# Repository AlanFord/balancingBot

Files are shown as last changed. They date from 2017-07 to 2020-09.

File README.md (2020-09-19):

# Balancing Bot
## Table of Contents
- [Introduction](#introduction)
- [The Remote Control](#the-remote-control)
	- [Wiring the Nunchuck](#wiring-the-nunchuck)
	- [Wiring the Transceiver](#wiring-the-transceiver)
	- [Putting It All Together](#putting-it-all-together)
	- [Powering It Up](#powering-it-up)
	- [Programming the Arduino](#programming-the-arduino)
- [The Bot](#the-bot)
	- [Hardware](#hardware)
		- [The Frame](#the-frame)
		- [The Motors and Wheels](#the-motors-and-wheels)
		- [Motor Control](#motor-control)
		- [Balancing](#balancing)
		- [Power](#power)
		- [Communications](#communications)
		- [The Blinky Lights](#the-blinky-lights)
		- [The Brains Behind it All](#the-brains-behind-it-all)
	- [Software](#software)
		- [Function List](#function-list)
		- [Timing Overview](#timing-overview)
		- [Battery Voltage Monitoring](#battery-voltage-monitoring)
		- [Attitude Monitoring](#attitude-monitoring)
		- [Wireless Communications](#wireless-communications)
		- [Serial Communications](#serial-communications)
		- [Motor Control Software](#motor-control-software)
		- [The Feedback Calculations](#the-feedback-calculations)
- [Operating the Balancing Bot](#operating-the-balancing-bot)
	- [Calibrating the Accelerometer](#calibrating-the-accelerometer)
	- [Starting up the Robot](#starting-up-the-robot)
	- [If Something Goes Wrong](#if-something-goes-wrong)

## Introduction
The Balancing Bot is a battery-powered two-wheeled balancing robot that can move under remote control.  The robot is built primarily from off-the-shelf parts.  The frame is plywood, easily made with hand tools or a small CNC router.  The robot’s electronics are based on an Arduino microcontroller and a combination gyro/accelerometer.  Communications with the remote control are performed over a 2.4 GHz wireless transceiver module.  The remote control is comprised of a repurposed Wii-compatible nunchuck controller, an Arduino microcontroller, and a 2.4 GHz wireless transceiver module.

This is a fork of the Joop Brokking's 
[balancing robot](http://www.brokking.net/yabr_main.html).
Many parts have been replaced with easier-to-obtain (for me) breakout boards from sparkfun.com, pololu.com, and amazon.com.

## The Remote Control
The primary component of the remote control is the Wii-compatible nunchuck.  The nunchuck joystick is used to maneuver the robot in right, left, forward, and backward movements.  The nunchuck is designed to communicate via a proprietary I2C connection.  Fortunately, it’s easy to communicate with the nunchuck using and Arduino Uno.  The Arduino programming environment provides a library (Wire) that implements the I2C communications protocol.

Getting the maneuvering commands from the remote control to the robot is performed using a Nordic Semiconductor nRF24L01+ 2.4 GHz wireless transceiver.  The communications protocol is proprietary, but the transceiver is available on a Sparkfun breakout board and communication is handled via the SPI and RF24 libraries.

Wiring the nunchuck to the Arduino can be plug-and-play if you use one of the various Wii nunchuck 
[breakout adapters](https://www.adafruit.com/product/345).  
However, the nunchuck can also be wired directly to the Arduino by removing the nunchuck connector.  This will be covered next.

### Wiring the Nunchuck
Removing the nunchuck connector reveals five wires, only four of which are required here - VCC (+3.3V), GND, SDA (data), and SCL (clock).  Unfortunately, the color of the various wires may change depending on the nunchuck supplier.  However, as a fallback the various wires can be identified by looking straight into the connector.  The wire layout would be as follows:

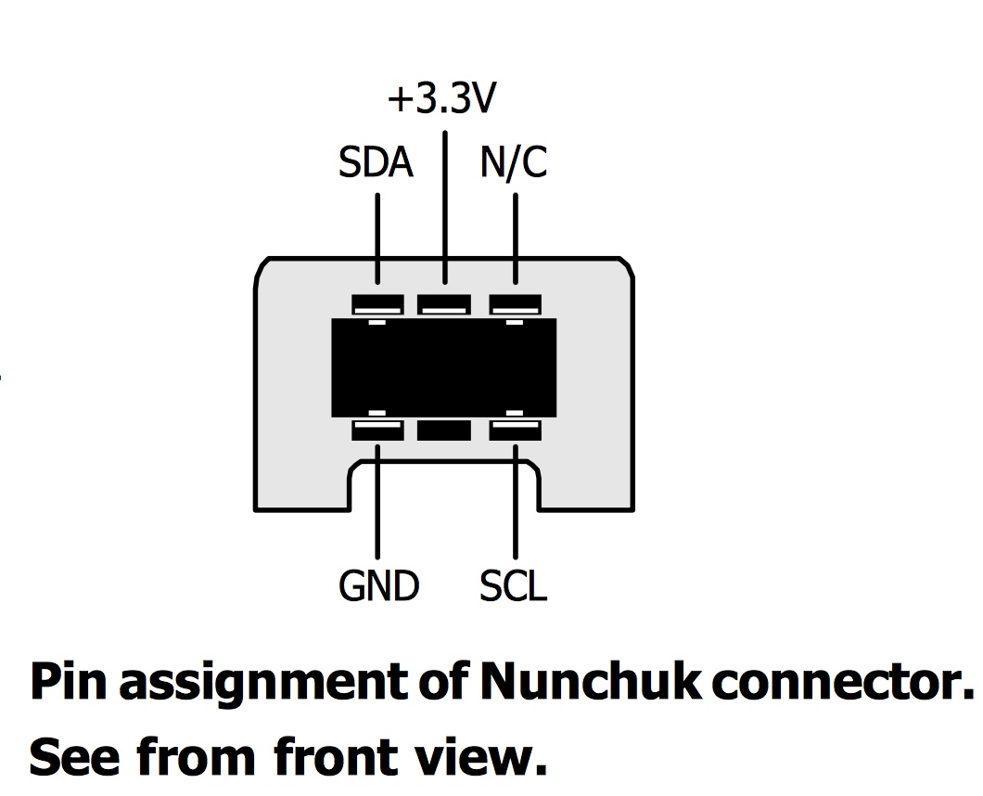
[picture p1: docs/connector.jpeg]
nunchuck-connector


Go ahead a cut off the connector and attach the wires to the following pins on an Arduino Uno – 

| Wii  | Arduino Pin |
| ---- | ---|
|SDA | A4 |
|SCL | A5 |
|+3.3V | 3V3 |
|GND | GND |

Note that the Wii nunchuck is a +3.3V device and the Arduino is a +5V device.  This is accommodated because an I2C connection is *open-drain*, i.e. the data lines (SDA and SCL) are nominally either grounded or floating.  The Wii nunchuck has internal pull-up resistors that will pull each data line up to +3.3V when either the Nunchuck or the Arduino is not pulling the line to ground during signaling.

However, the Arduino also contains internal pull-up resistors that are enabled by default and will attempt to pull the signal lines up to +5V.  While this appears not to damage the nunchuck, it would be more appropriate to disable the Arduino internal pull-up resistors and rely only on the pull-ups internal to the nunchuck.

### Wiring the Transceiver
The transceiver that I used was part of a Sparkfun breakout board that used an SPI interface.  The SPI interface requires more data lines than an I2C or serial connection.  The following are the required connections:

| Transceiver | Arduino Pin |
| --- | --- |
|CE | D9 |
|CSN | D10 |
|MOSI | D11 |
|MISO | D12 |
|SCK | D13 |
|VCC | 5V |
|GND | GND |
|IRQ | not used! |

### Putting It All Together
While all of those wires could be just attached to the Arduino Uno headers, it didn’t seem to make for stable connections.  In addition, it would be best if the wireless transceiver stood up vertically above the Arduino Uno to provide better radio reception.  My solution was to use an Arduino prototyping shield.  A female 8-pin header was soldered to the prototyping shield and a male right-angle 8-pin header was soldered to the transceiver board.  Plugging the transceiver into the female header on the prototyping shield allows the transceiver to stand upright above the Arduino Uno.  The nunchuck wires can be soldered directly to the appropriate locations on the prototyping shield.  I mounted the Arduino Uno on a 
[plastic mounting plate](https://www.adafruit.com/product/275)
 that provided an area to the side for securing the nunchuck cable with a cable tie and an adhesive-backed mounting base.

### Powering It Up
The remote control can be powered by a power supply with a barrel jack supplying between +9V and +12V.  Alternatively, it can be powered from a laptop via a USB connector.

To make the remote control more portable, it is possible to power it via a USB cable attached to a cell-phone battery pack.  Care must be taken to choose a batter pack that does not shut off when the current flow drops to about 20 mA (typical of the Arduino Uno).  If you have a battery pack that does tend to shut off, adding an LED to the Arduino that uses an additional 15 mA may keep the battery pack from shutting off.

### Programming the Arduino
The Arduino Uno program reads the state of the nunchuck joystick and transmits the state to the robot.  The Uno program is *Balancing_robot_remote.ino*.  When first powered up, the program initializes the microcontroller by making calls to the routines `initialize_serial()`, `initialize_radio()`, `initialize I2C()`, and `wake_nunchuck()`.  `initialize_serial()` inizializes a 9600 baud serial connection that can be optionally be used to monitor the state of the Uno.  `initialize_radio()` and `initialize I2C()` are self explanatory.  `wake_nunchuck()` initializes the I2C data communication with the nunchuck.  Of special interest are the lines in `initialize_I2C()` that disable the Arduino internal pull-up resistors.  This configuration permits safely connecting the +3.3V nunchuck with the +5V Arduino.  The relevant lines in `initialize_I2C()` are:

```cpp
Wire.begin();			//Start the I2C bus as master
digitalWrite(SCL, LOW);		//disable the pull-up on the SCL line
digitalWrite(SDA, LOW); 	//disable the pull-up on the SDA line
```

SCL and SDA are Arduino-defined constants referring to the appropriate pins.

Initializing the radio requires using a “pipe” address, or name. We need to ensure that the remote and the robot are on the same pipe address.  The pipe address is a five-character string – in this case “1robt”.

Communicating with the nunchuck consists of sending 0x00 to the nunchuck followed by a request for six bytes of data.  The first byte of data received represents the left/right position of the joystick, with the values varying from 0 to 255 (full left to full right).  The second byte of data received represents the front/back position of the joystick, with values varying from 0 to 255 (full reverse to full forward).  Ignoring a dead zone of 80 to 170 (to avoid jitter and noise), the nunchuck data is converted to robot commands of BOT_LEFT, BOT_RIGHT, BOT_FORWARD, and BOT_REVERSE.  The commands are represented by the following byte encoding:

```
BOT_LEFT            B00000001
BOT_RIGHT           B00000010
BOT_FORWARD         B00000100
BOT_REVERSE         B00001000
BOT_STABLE          B00001100
```

The values can be combined by ORing the bytes together.  For example, to move forward and turn right simultaneously the values of BOT_FORWARD and BOT_RIGHT would be ORed together to form a command byte of B00000110.

The command byte is then broadcast via the transceiver using the library call radio.write(). After a delay of 40 milliseconds the process is repeated.

## The Bot
It takes a lot to keep the robot upright and doing it’s job.  The robot runs on two wheels, powered by one stepper motor for each wheel.  Controlling the direction of wheels independently allows the robot to roll forward, roll backward, turn right, turn left, or a combination of these.  In addition to the overall motion of the robot, the wheels are also used to balance the robot.  If the accelerometer indicates that the robot is tipping forward or backward, the wheels are driven to move the wheels in the direction of the tilt, effectively moving the robot body into an upright positon.  The ability to do this without having the top of the robot flailing around requires that a weight be added to the top of the robot, simulating an “inverted pendulum”.  In this case the weight is implemented by mounting a large lithium-polymer (LiPo) battery on the top of the robot frame.  Beyond helping balance the robot, the size of the LiPo batter also provides a substantial power supply for the robot’s electronics and motors.

The robot also needs computing power, but an Arduino Uno (the microcontroller used in the remote control) is too large to use on the robot.  Instead, an Arduino Pro Mini is used.  The Pro Mini is significantly smaller and comes in 3.3 V and 5 V versions.  Only the 5V version should be used, as 5V is need to interface with some of the electronics.  This will be covered in more detail later.

### Hardware

#### The Frame
Wood.  Just wood.  Well, maybe a little fancier than usual.  The frame is built out of  “baltic birch” plywood.  This plywood has more plies (layers) than your average plywood, making it stronger, flatter, etc.  The various pieces of the frame are held together with wire brads from a brad nailer.  Hand nailing will work also.

#### The Motors and Wheels
The robot moves because of stepper motors attached to wheels.  The stepper motors used in this project are NEMA 14-size bipolar motors from STEPPERONLINE (part number 14HS13-0804S).  The motors had the following characteristics:

```
18 N-cm (25.5 oz.-in) holding torque
1.8 degree stepper angle (200 steps/rev)
5.4V, 0.8A
6.8 ohms
5 mm shaft diameter
24 mm shaft length
```

The motors are mounted directly to the wooden robot body using the four threaded mounting holes found on the face of all NEMA stepper motor bodies.

Wheels can be found from many sources or may be repurposed from old toys.  The wheels used in this project were 60mm x 8mm with silicone tires.  The wheels were mounted to the stepper motor shafts using Pololu aluminum mounting hubs sized for a 5mm stepper shaft.

#### Motor Control
The stepper motors are controlled by stepper motor drivers, one per motor.  The stepper motor drivers receive motor positioning signals from a microcontroller and convert them into motor coil currents to control the motors.  This design uses two of the Pololu A4988 Stepper Motor Driver.  This driver can operate from 8 V to 35 V and can deliver up to 1 A per phase without a heat sink.  Microstepping down to 1/16-step is available.  VDD can be in the range of 3 V – 5.5 V.  Current limiting (the motors in use can only take 800 mA) is performed by adjusting an on-board trimmer potentiometer.  After adjusting the potentiometer, the current limit is

```
Current limit = VREF / (8 x 0.068 ohms)
```

where VREF is the voltage on the trimmer dial (measure by lightly touching – pressing down can change the trimmer pot adjustment!) or at the neighboring via.  For example measuring 0.5 V with a reference voltage of 5 V would mean a current limit of 0.919 A.  As the motors can take a maximum of 800 mA, the measured voltage should never be greater than 0.435 V, assuming a reference voltage of 5 V.  The original design indicates a current limit of 150 mA was to be used.  The modified design used here needs about 500 mA to power the motors such that they will hold position.

The following is a general depiction of how the motor driver should be wired.

![A4988]

Additionally, the \~ENABLE pin should be raised to the logic power supply voltage to disable the driver.  MS1, MS2, and MS3 
can be used to control microstepping as follows:

| MS1  | MS2  | MS3  | Microstep Resolution |
| ---- | ---- | ---- | --- |
| Low  | Low  | Low  | Full step |
| High | Low  | Low  | Half step |
| Low  | High | Low  | 1/4 step |
| High | High | Low  | 1/8 step |
| High | High | High | 1/16 step |

The motor drivers used in the robot are wired as follows:

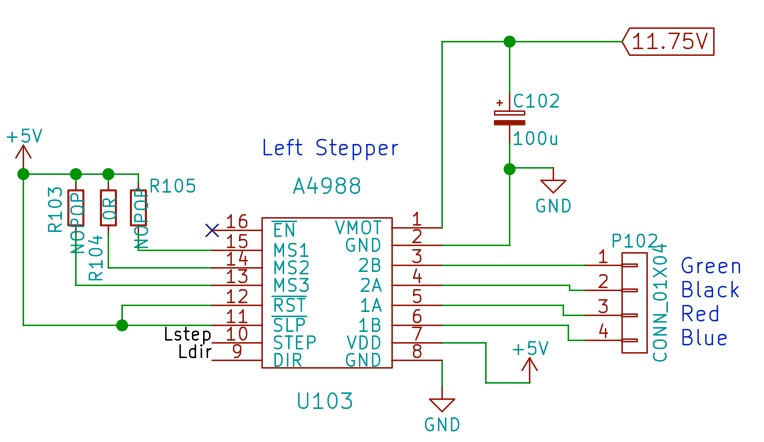
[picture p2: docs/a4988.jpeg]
A4988-wiring


Only MS2 is High, so the microstepping is set to ¼ step.  The \~ENABLE line is not connected; hence the stepper driver is always enabled.  The STEP and DIR pins are connected to the following Arduino Pro Mini pins:

|            | Arduino Pins | Arduino Pins |
|            | for          | for          |
| Driver Pin | Left Motor   | Right Motor  |
| ---------- | ------------ | ------------ |
| STEP       |	D4          | D2           |
| DIR        |	D5          | D3           |

#### Balancing
Balancing of the robot is performed by monitoring the gyro/accelerometer.  The gyro/accelerometer is implemented using a MPU-6050 six-axis sensor on a GY-521 breakout board.  The GY-521 communicates over I2C and can be powered with between 3.3V and 5V.

Care should be taken when mounting the GY-521 to the robot.  The accelerometer X-axis should be the vertical axis with the Y-axis pointing to the left as you face the front of the robot.  Mounting in other orientations will require software changes.

Wiring up the GY-521 is straight forward – 

| GY-521 | Arduino Pro Mini Pin |
| --- | --- |
| SDA | A4 |
| SCL | A5 |
| VCC | 5V |
| GND | GND |

#### Power
Power ultimately comes from a 3S LiPo battery, used not only for power but also to add weight to the top of the robot for balancing.  Power control and polarity are provided by a toggle switch and a diode.  The battery voltage is regulated down to 5V using a D24V10F5, 5V, 1A step-down voltage regulator available from pololu.com.  5V is then supplied to all of the on-board electronics.  The +11.75V output of the diode is supplied to the motor drivers to power the stepper motors.  The following summarizes the power supply:

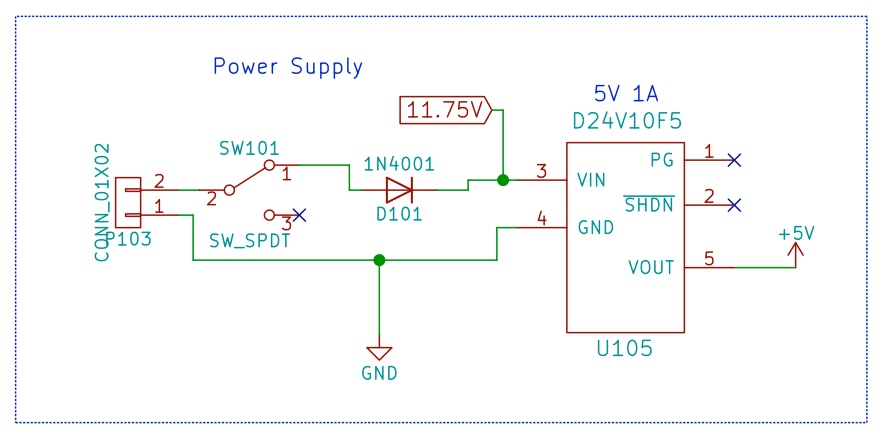
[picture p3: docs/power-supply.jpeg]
power-supply


#### Communications
The robot uses the same nRF24L01+ 2.4 GHz wireless transceiver used by the remote control.  The following are the required connections:

| Transceiver | Arduino Pin |
| --- | --- |
| CE | D09 |
| CSN | D10 |
| MOSI | D11 |
| MISO | D12 |
| SCK | D13 |
| VCC | 5V |
| GND | GND |
| IRQ | not used! | 

#### The Blinky Lights
One status LED is used on the robot.  A red LED is connected is series with a 330 ohm resistor between the Arduino D17 pin and ground.  Of course, I forgot to add this LED originally so my robot has it bodge-wired into place.  

The LED is first used when the robot is initially powered on.  The robot should be laying on it’s back when the power switch is toggled.  The LED will begin blinking as the accelerometer is calibrated.  Once the blinking stops, slowly rotate the robot to vertical and it will stabilize.

The other use of the LED is to warn when the battery voltage is too low.  The LED will turn on continuously when the battery voltage drops below +10.5V.  At this point the motors will also be de-energized and the robot will stop.

#### The Brains Behind it All
Integrating the robot parts is the job of the Arduino Pro Mini.  The Arduino Pro Mini comes in both a 3.3V and 5V version, but the 5V version should be used here so the voltage is consistent with the supply voltage used by the transceiver and the motor drivers.

### Software
The Arduino provides several functions, namely attitude monitoring, motor control, communications with the remote, and battery voltage monitoring.  These will be described in the following sections.  As an introduction though, it should be clear that the Arduino separates work into two categories – setup and loop.  Work performed in the setup occurs only once after power-up.  Work performed in the loop is repeated until the robot is powered down.  Some of the robot functions are performed in the setup and some are controlled by the loop.

#### Function List
- Balancing_robot.ino
  	- void setup(), the Arduino setup routine
	- void loop(), the main Arduino control loop
- misc.ino
	- void initialize_i2c(), initialize the i2c bus to communicate with the remote
	- void initialize_timer(), initialize the timer used with the interrupt service
	- bool battery_voltage_is_low(), determine if the battery voltage is too low
- gyro.ino
	- void initialize_gyro(), initialize the gyro/accelerometer
	- void calibrate_gyro(), initial gyro calibration
	- void get_gyro_angle(), determine the gyro's estimate of the vertical angle
	- float get_accelerometer_angle(), determine the accelerometer's estimate of the vertical angle
- radio.ino
	- void initialize_radio(), initialize the RF24 radio transceiver
	- byte get_radio_data(), get a byte of data from the remote control
- pid.ino
	- float pid_calculator(), determine the pid feedback value
	- void direction_control(), add user direction signal to pid feedback value
	- void calculate_motor_pulse_interval(), conver pid result to motor period
- isr.ino
	- ISR(), drive the stepper motor based on requested motor period

#### Timing Overview
The various processes that make up the control software work on a number of timing intervals.

- The remote control has a primary timing loop that is executed once every **40 milliseconds**.  This is the
frequency at which the handheld controls are polled for updates and new data are transmitted to the robot.
- Data received from the remote control by the robot is considered valid for only **100 milliseconds** if no other data is received.  After that time it is discarded.  This avoids the issue of using old, invalid commands when the radio link is interrupted.
- The robot has a primary timing loop that is executed once every **4 milliseconds**.  This timing loop 
controlls the frequency at which the gyro is checked, incoming remote control commands are logged, 
and balancing control calculations are updated, and motor speeds are determined.
- The time interval for the primary timing loop is also used to calculate the change in robot angle during the last loop interval (**4 milliseconds**).  The gyro only determines the *rate* of change in the angle.  The time interval is used to determine the change in the angle.
- The interrupt routine that drives the motors executes every **20 microseconds**.  The stepper motor drive 
period is comprised of one interrupt period executing a motor step followed by several non-stepping interrupt periods.

#### Battery Voltage Monitoring
The battery voltage is being monitored on pin A0, an analog input.  The nominal voltage for a 3S LiPo battery is +11.1 V, a maximum voltage of +12.6 V, and the minimum operating voltage is 9.9 V.  There is a diode in the battery circuit to prevent hooking the battery up with the wrong polarity.  The voltage drop across the diode is approximately 0.85 V.  Hence the remaining maximum voltage is +11.75 V and the minimum voltage would be +9.05 V.  Unfortunately the Arduino can only measure voltages between 0 V and 5 V.  Two resistors can be used to create a voltage divider to reduce the voltage to no greater than +5V.  The maximum voltage needs to be divided by at least (+11.75 V)/(+5 V) = 2.35.  Using readily available resistor sizes, a voltage divider can be made from 33K ohm and 21.5K ohm resistors, for a divider of (33K + 21.5K)/21.5 = 2.535.  Now the maximum voltage would be +11.75 V/2.535 = +4.64 V.

When reading the A0 pin, the Arduino generates an integer value of 0 for 0V and 1023 for 5V, or 0.00489 V per division.  Thus the integer generated from reading the pin would be

```
A0 = (battery voltage – 0.85V)/2.535/(0.00489V/division), or
A0 = (battery voltage * 80.67) – 68.57
```

Now, reading A0 with values between 0 and 1023, it’s hard to tell what the voltage really is.  So flipping the equation around and multiplying by 1000 (to get millivolts), we get

```
voltage reading = (A0+68.57)/80.67*1000 = A0*12.4 + 850
```

If the voltage reading drops below 10500 (+10.5V) the LED is turned on and the motors are de-energized.  The batter check is performed in the main loop of the Arduino software, executed on a 4 millisecond interval.

#### Attitude Monitoring
So why include both gyro and an accelerometer?  The gyro can determine the rate at which the robot is rotating (i.e. falling).  How is the gyro used to determine the angle of the robot?  The gyro’s value for rotation (degree/sec) is multiplied by the time since the last check to determine how much the robot’s angle has changed over that time.  But changed from what?  The gyro can’t determine what angle the robot started at.  This is where the accelerometer comes in.  When the robot is moved to an upright position, the accelerometer can tell from the gravitational pull how close the robot is to vertical.  Once the robot is close to vertical the angle calculated from the accelerometer is used to initialize the gyro’s ongoing, updated angle calculations.  Voila!

The gyro/accelerometer (henceforth referred to as the gyro) is initialized in the Arduino’s setup() function.  The gyro operating mode is set to 250 degree/sec full scale for the gyro and +/- 4g full scale for the accelerometer.  Both the gyro and accelerometer functions return a signed 16-bit integer.  The accelerometer has a sensitivity of 8192 LSB/g.  The gyro has a sensitivity of 131 LSB/degree/sec.

The gyro yaw and gyro pitch values are read from the gyro and then the program is paused for \~4 milliseconds.  This is repeated for a total of 500 times and the resulting yaw and pitch values are averaged over the 500 values.  The resulting average yaw and average pitch are the gyro calibration values.

In the main loop the gyro angle is initialized to equal the accelerometer angle only once, at the beginning of operation when the robot is standing vertical.  The gyro angle is then updated once every \~4 milliseconds (the loop time for the main program loop).

#### Wireless Communications
As with the remote control, communications with the wireless transceiver is done with the SPI bus.  As with the remote control, the radio is initialized with a pipe address of “1robt”.  Interestingly, while the radio can transmit on only one pipe, it can receive on six pipes simultaneously.  Thus when initializing the radio we must also specify a pipe number, in this case “1”.    Wireless communications occur in the main loop of the Arduino software, executed on a 4 millisecond interval.

#### Serial Communications
Serial communications can be enabled at compile-time by defining the macro SERIALCOMM.  Serial communications are then initiated at 9600 baud (slow enough not to impede the other work being done).  Serial communications occur over the USB connection.

#### Motor Control Software
Motor control is not done in either of the normal Arduino functions setup() or loop().  Instead, motor control is performed in an interrupt handler.  The Arduino has built-in timers that can cause the microcontroller to perform operations on a repeating fixed interval.  One of the ways this can be done is to associate a special program (i.e. a function) with the timer.  Such a program/function is referred to as an interrupt handler.  The robot uses Timer 2 to perform motor control on an interval of every 20 microseconds.  The motor control is performed by a function called ISR(TIMER2_COMPA_vect).  Timer 2 is initialized in the standard Arduino setup() function.

Moving the stepper motor by one step (or by a ¼ step in this configuration) a pulse is generated on the appropriate input pins for the stepper controllers.  This is done by pulsing Arduino Pro Mini pin D2 for the right motor and pin D4 for the left motor.
Some caution is needed when controlling the direction of the stepper motors.  The stepper motors and drivers are configured symmetrically with respect to the Arduino Pro Mini.  However, the left motor is rotated 180 degrees when mounted on the robot.  Thus, the right motor will go forward when Arduino pin D3 is high and reverse when pin D3 is low.  The left motor is reversed, going forward when Arduino pin D5 is low and reversing when pin D5 is high.

Manipulating the Arduino Port D pins for motor stepping and direction is made a little easier by the constants defined in the Arduino program:

```cpp
const uint8_t LEFTMOTORDIR     = (0b00000001 << 5);
const uint8_t LEFTMOTORSTEP    = (0b00000001 << 4);
const uint8_t RIGHTMOTORDIR    = (0b00000001 << 3);
const uint8_t RIGHTMOTORSTEP   = (0b00000001 << 2);
```

#### The Feedback Calculations
The feedback calculations are designed to continuously update the motor positioning required to accomplish several (sometimes mutually exclusive) goals simultaneously.  The goals are:
 - Keep the bot vertical and stable when not moving.  This is accomplished by adjusting the variable `self_balance_pid_setpoint`

 - Incorporate necessary changes when the remote control requests a turn.  This accomplished by setting the variables `pid_output_left` and `pid_output_right` to be +/- `turning_speed`.  The sign is adjusted to make the wheels turn in opposite directions, spinning the robot in place.  The `turning_speed` variable is a predefined constant (20).

 - Incorporate changes when the robot is to move forward or backward.  To move forward, the robot is leaned forward by adjusting pid_setpoint in 0.005 increments each time the main loop is executed (4 millisec) until the maximum speed `max_target_speed` (150) is reached.

  - If the robot is more than 30 degrees from vertical (i.e. it fell over), shut the motors down and reset the feedback calculations.

  - When the robot is not at the required angle from vertical, calculate a new.

As was mentioned in the Motor Control section, the interrupt handler is executed every 20 microseconds.  The motor step pulse is activated in one interrupt and deactivated in the next.  Thus, the minimum pulse period (the full cycle) is 40 microseconds and the step frequency is 25,000 steps/sec.  The motors are nominally 200 steps/rev and the motor controllers are set for ¼ microstepping, so the maximum speed of the robot is 

```
(25,000microsteps/sec)(1step/4microsteps)(1rev/200steps) = 31.25 revolutions/sec
 ```

The wheels/tires have a diameter of 60 mm, resulting in a maximum linear speed of

```
31.25 rev/sec * (pi * 60 mm) = 5890.5 mm/sec = 19.3 ft/sec.
```

`throttle_left_motor` and `throttle_right_motor` are generated by the feedback calculations to control the motor.  They contain the number of 20 microsecond intervals between the pulses used to move the stepper motor.  A counter for each motor counts up to the throttle value from 0.  On 0 the stepper pulse is created and on 1 the stepper pulse is ended, giving one 20 microsecond pulse followed by a (throttle-1) * 20 microsecond delay.  A negative value of throttle_left_motor or throttle_right_motor will cause the motor to reverse.

In summary, it’s important to remember that the value generated by the feedback calculations is the *delay* between stepper motor steps.

## Operating the Balancing Bot

### Calibrating the Accelerometer
This really only has to be done once, so I’m putting it in a separate section of the documentation.

### Starting up the Robot
It’s pretty simple; just follow these steps:

 1.	Power up the remote, either using a wall wart or a battery pack
 2.	Lay the robot on it’s back on a flat surface.
 3.	Flip the toggle switch to power-up the robot.
 4.	Wait for the gyro/accelerometer to calibrate (the red LED will stop blinking)
 5.	Gently rotate the robot to a vertical position
 6.	Turn it loose and start driving it around!

### If Something Goes Wrong 
If the robot falls down because it ran into something, just pull it back upright and it should stabilize itself.

If, during operation, the red LED turns on, the motors will de-energize because the LiPo battery voltage has dropped too low.  Flip the toggle switch to turn off the robot, swap in a new battery, and begin again!

<!-- Images -->
[nunchuck-connector]:   ./docs/connector.jpeg      "Nunchuck connector wiring"
[A4988]:                ./docs/basic.png           "A4988 diagram"
[A4988-wiring]:         ./docs/a4988.jpeg          "A4988 wiring diagram"
[power-supply]:         ./docs/power-supply.jpeg   "Power supply diagram"

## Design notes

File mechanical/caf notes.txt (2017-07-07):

Website: http://www.brokking.net/yabr_main.html

Board List
==========
Arduino pro mini, 1, https://www.amazon.com/Arduino-Pro-Mini-328-3-3V/dp/B004G53J6M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
Arduino Uno, 1 [already in hand?]
FTDI USB to TTL programmer for Arduino pro mini, 1, [already in hand?]
MPU-6050 gyro and accelerometer, 1, https://www.amazon.com/Kootek-MPU-6050-MPU6050-sensors-Accelerometer/dp/B008BOPN40
2.4G wireless serial tranceiver module, 2
Geeetech StepStick DRV8825, 2, https://www.pololu.com/product/2133
Mini DC 7~28V to DC 5V step-down converter, 1

Hardware
========
Stepper Motor, 2
Wired nunchuck controller for Wii, 1, https://www.amazon.com/Supersaving360-Nunchuck-Nunchuk-Controller-Nintendo/dp/B00JFOZX3Q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
11.1V 2200mAh 30C Li-polymer Battery, 1, https://www.amazon.com/Battery-Helicopter-Quadcopter-Multirotor-EFLB22003S30/dp/B013TK47VK
B3AC 2s/3S Lipo balance charger

Details
=======
Stepper Motors
	Nema 14
	1.8 Degree step angle
	Bipolar (equivalent to 2 phase?)
	3.6V DC
	1.2A/phase
	8.8 ohms/phase
	3.5 mH
	185 mN.m Min holding torque (18.5 Ncm) (26 oz-in)
	31 g.cm2 rotor torque
	190g (6.7 oz)
	Brand:  Geeetech Model 35BY
	1.39in x 1.39 in x 2.48 in

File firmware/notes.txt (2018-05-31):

Changes from the original design:
1) Using SPI to communicate with the wireless card.  This will require use of arduino
	pins D10, D11, D12, and D13.
2) Need to solder up another LED.  The on-board LED is attached to the ATMEGA328 pin 17 
	(PB5) (SCK), which is wired to pin 9 of JP6.  This appears to be labeled on the 
	Arduino Pro Mini board as D13.
3) The voltage divider was redone, so the constants in the code should be altered.
4) Serial to the PC may be available since the wireless link isn't using it.

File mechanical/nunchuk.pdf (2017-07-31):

## Wii

## Nunchuk

## Interface

The

Wii

Nunchuk

uses a

proprietary

connector

with

six pins.

The

connections

are

as
follows.

Figure

1:

Wii

Nunchuk

Pinout
To

communicate

with

the

Nunchuk,

we

must

send

a

handshake

signal.

If

you

are
using

a

black Wii

Nunchuk,

send 2

bytes

0xF0, 0x55 to

initialize the first

register
and

0xFB, 0x00 to

initialize

the

second

register

of

the

Nunchuk.

On

a

white

Wii
Nunchuk,

send

0x40, 0x00 followed by 0x00. The I²C

address

of

both

Wii

Nunchuks
is

0x52.

The

frequency

used

to

communicate

with

the

Wii

Nunchuk

is

100KHz.

1 3 5
2 4 6
1 = +3V (3V recommended but works at 5V) | 2 = Clock
3 = N/A | 4 = N/A
5 = Data | 6 = Gnd

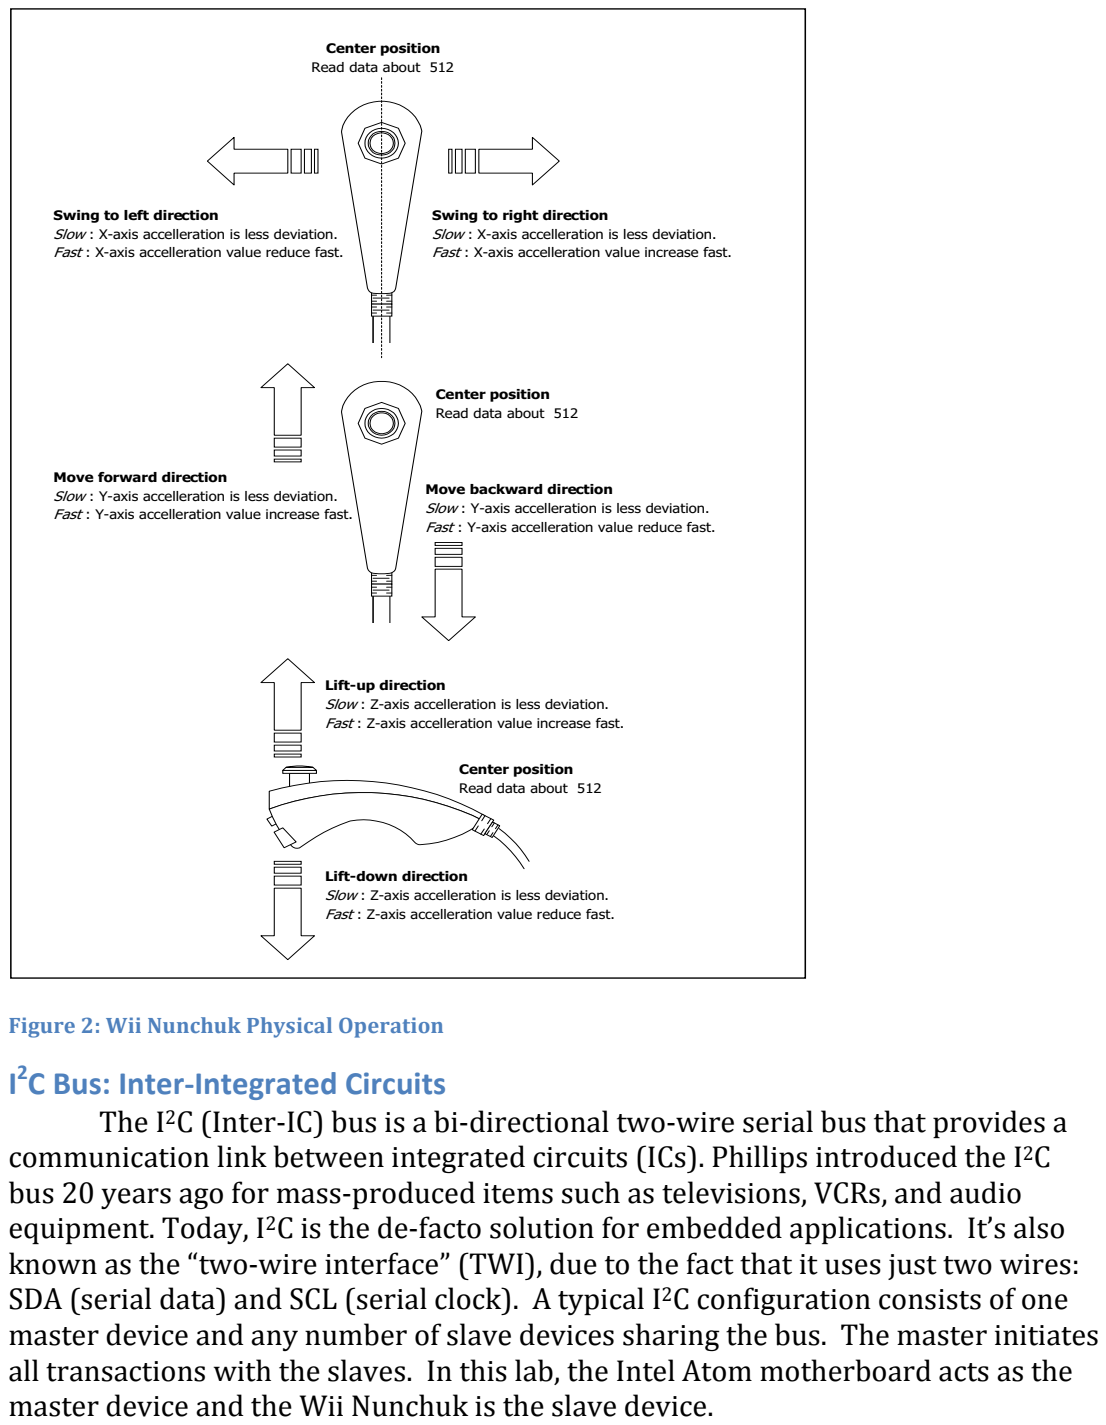
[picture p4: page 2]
Figure; Wii; Nunchuk; Physical; Operation; Bus:; Inter-‐Integrated; Circuits; The; I²C; (Inter-‐IC); bus; bi-‐directional; two-‐wire; serial; bus that; provides; communication; link; between; integrated; circuits; (ICs).; Phillips; introduced; the; years; ago; for; mass-‐produced; items; such; televisions,; VCRs,; and; audio; equipment.; Today,; de-‐facto; solution; embedded; applications.; also; known; “two-‐wire; interface” (TWI),; due; fact; that; uses; just; two; wires:; SDA; (serial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

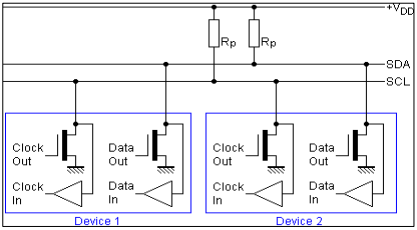
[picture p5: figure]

Another

name

you

will

hear

used

in

connection

with

I²C

is

SMBus (System
Management

Bus).

The

SMBus

protocol

was

developed

by

Intel

in

2005 and

is

based
on

I²C.

SMBus

defines

a

stricter

range

of

operating

limits,

including

clock

speed,
timing

and

data

formats,

compared

to

I²C.

Many

I²C

devices

have,

in

turn,
incorporated

policies

from

SMBus

and

both

kinds

of

devices

can

often

be

used

on
the

same

bus.

Figure

3:

I²C

Device

Circuit

Wii

Nunchuk

Output

The

Wii

Nunchuk

is

a

slave

I²C

bus

device

that

outputs

six

bytes

of

data

as
follows.

Figure

3:

Wii

Nunchuk

I²C

Output

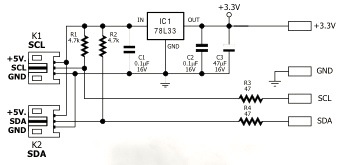
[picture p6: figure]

Figure

4:

Nunchuk

Interface

Board

Circuit

!&!!

!&!"

!&!'

!&!(

!&!)

!&!*

+,-./01234

+,-./01235

6117879,:7/79343;<0/3=3/,3<0/3'3>,93"!?<0/397.,8@/0,AB

6117879,:7/79353;<0/3=3/,3<0/3'3>,93"!?<0/397.,8@/0,AB

6117879,:7/793C3;<0/3=3/,3<0/3'3>,93"!?<0/397.,8@/0,AB

61178D3C
<0/3"

61178D3C
<0/3!

61178D35
<0/3"

61178D35
<0/3!

61178D34
<0/3"

61178D34
<0/3! | E?<@//,A | C?<@//,A
GH/H3<-/7397170I7 | 6FF97..
Byte 0x00 : | X-axis data of the joystick
Byte 0x01 : | Y-axis data of the joystick
Byte 0x02 : | X-axis data of the accellerometer sensor
Byte 0x03 : | Y-axis data of the accellerometer sensor
Byte 0x04 : | Z-axis data of the accellerometer sensor
Byte 0x05 : | bit 0 as Z button status - 0 = pressed and 1 = release
| bit 1 as C button status - 0 = pressed and 1 = release
| bit 2 and 3 as 2 lower bit of X-axis data of the accellerometer sensor
| bit 4 and 5 as 2 lower bit of Y-axis data of the accellerometer sensor
| bit 6 and 7 as 2 lower bit of Z-axis data of the accellerometer sensor

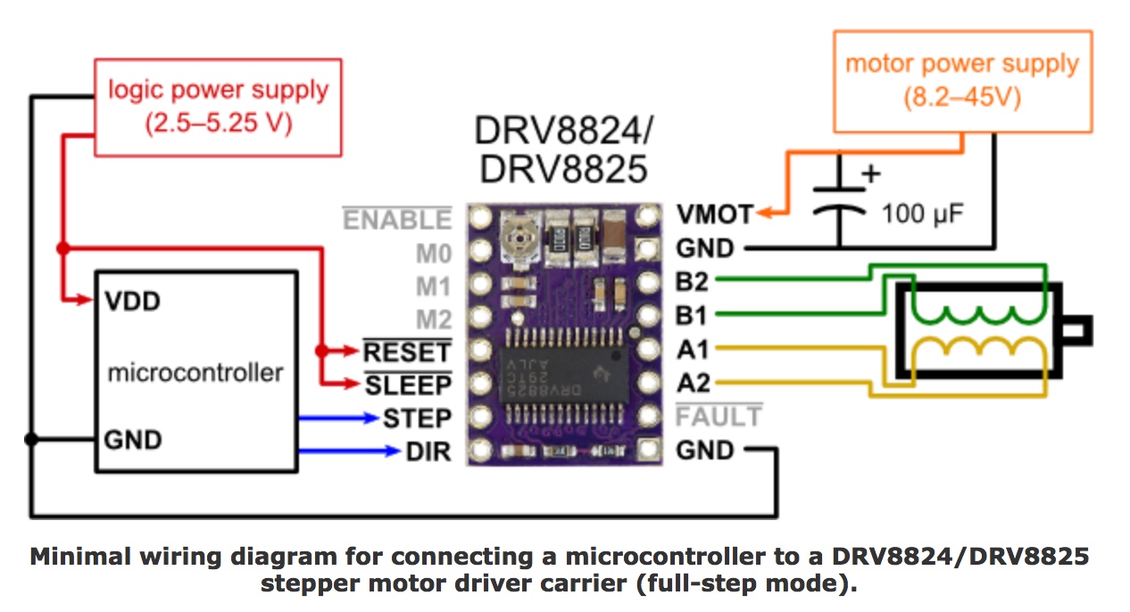
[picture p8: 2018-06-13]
docs/motor-driver.jpeg

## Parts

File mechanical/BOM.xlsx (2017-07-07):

 | Balancing Bot BOM
Count | Description | Part No. | Supplier | Status | Comment
1 | Arduino pro mini | DEV-11113 | sparkfun.com | basket | 5V, 16MHz, already own one?
1 | FTDI USB to TTL programmer |  |  |  | already own one?
1 | Arduino Uno |  |  |  | already own one?
1 | MPU-6050 gyro and accelerometer | B008BOPN40 | amazon.com | ordered | Kootek GY-521
2 | 2.4G wireless serial transceiver | WRL-00691 | sparkfun.com | received | nRF24L01+
2 | 35mm Stepper motor | B00PQ4Y9B6 | amazon.com | ordered | 0.8A/phase, 6R8, 18Ncm, 34mm long
2 | DRV8825 stepper driver | 2133 | pololu.com | ordered | 1.5A may be overkill
1 | wired nunchuck controller for Wii | B00JFOZX3Q | amazon.com | ordered
1 | 7-28V to 5V DC step-down converter | 2858 | pololu.com | ordered
1 | 11.1V 2200mAh 30C LIPO battery | B0072AEY5I | amazon.com | ordered | Turnigy 2200mAh 3S 20C Lipo, 6.6 oz, 103 x 33 x 24mm
1 | B3AC 2S/3S Lipo balance charger | 2588 | pololu.com | ordered | iMAX B6AC V2 Balance Charger - does it have the correct connector?
1 | PCB
1 | 3-pin toggle switch
1 | 2k2 resistor
1 | 3k3 resistor
1 | 4k7 resistor
1 | 1N4001 diode
1 | wheels (2) | 1421 | pololu.com | ordered
1 | wheel hardware (2) | 1203 | pololu.com | ordered | #4-40 screws not included
assorted | wood, 1/2"
assorted | wood, 1/8"
assorted | acrylic, 1/8"
 | standoffs
 | bolts
 | velcro tie-down
1 | arduino charger |  |  |  | already own one?
1 | LIPO batter tester monitor | B013U1CP08 | amazon.com | ordered

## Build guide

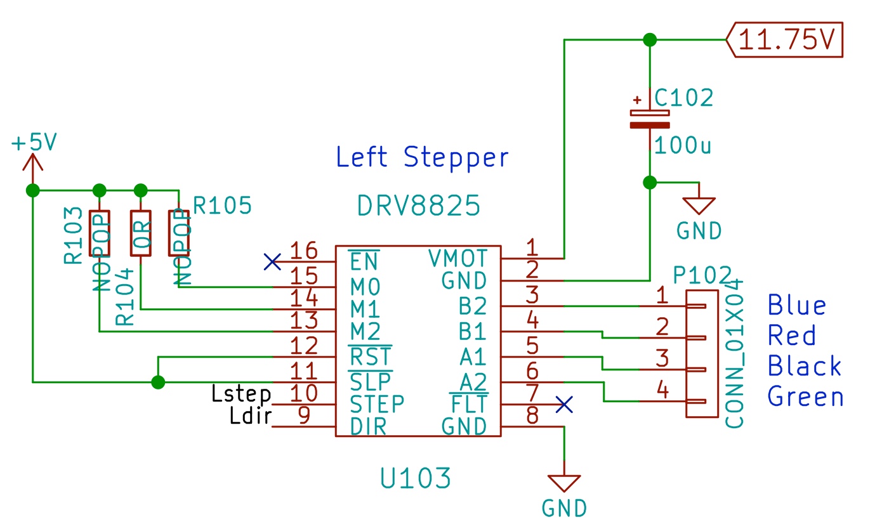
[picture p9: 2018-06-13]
docs/driver-wiring.jpeg

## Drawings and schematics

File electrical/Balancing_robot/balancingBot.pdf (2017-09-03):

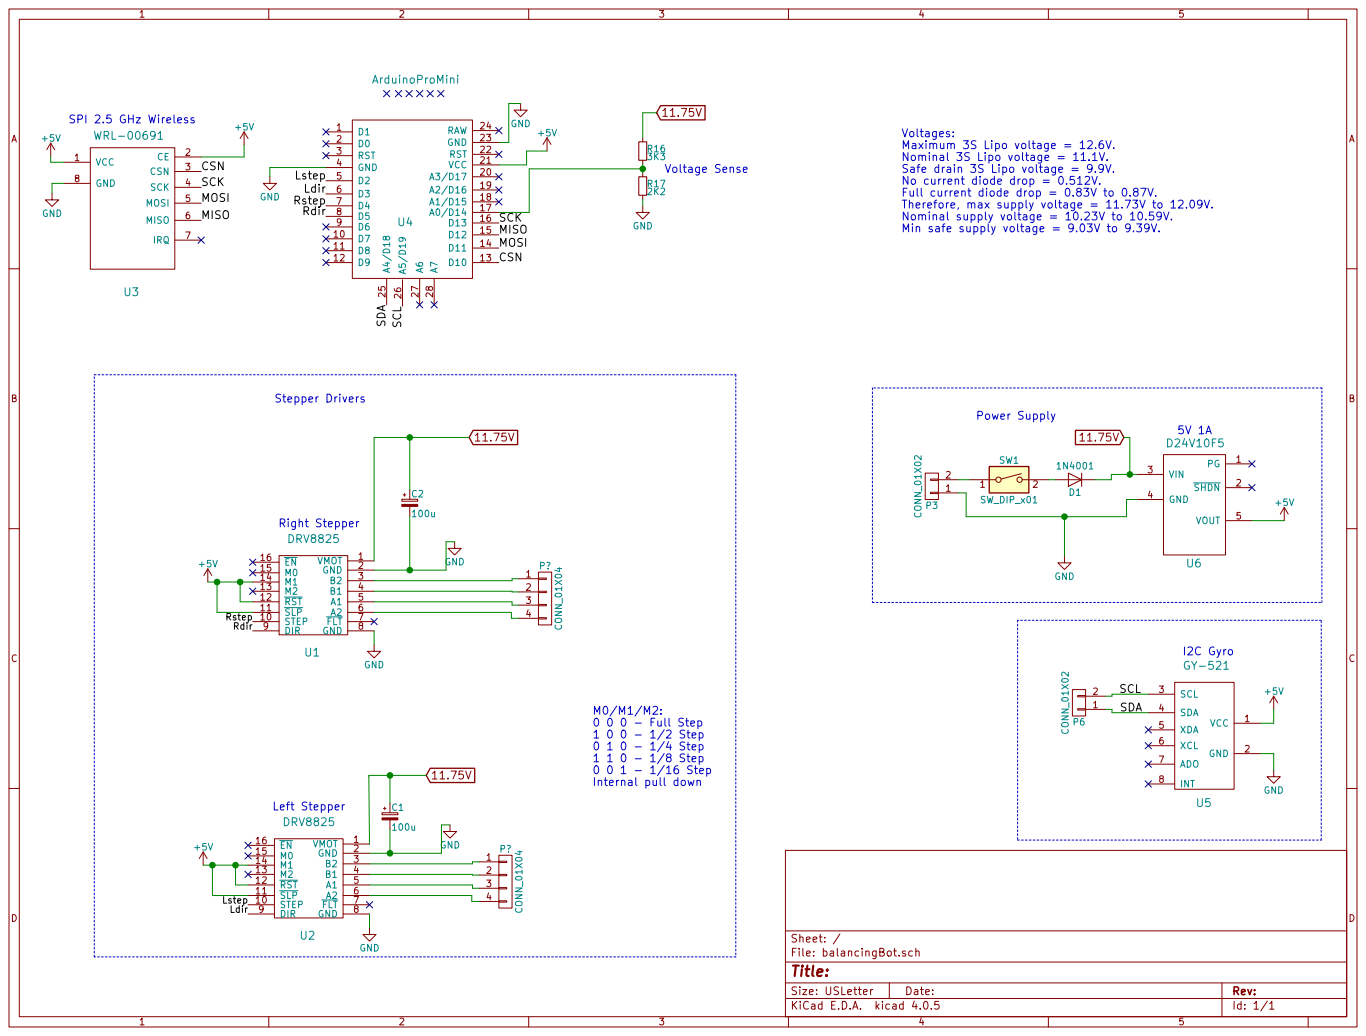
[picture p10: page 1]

Voltages:
Maximum 3S Lipo voltage = 12.6V.
Nominal 3S Lipo voltage = 11.1V.
Safe drain 3S Lipo voltage = 9.9V.
No current diode drop = 0.512V.
Full current diode drop = 0.83V to 0.87V.
Therefore, max supply voltage = 11.73V to 12.09V.
Nominal supply voltage = 10.23V to 10.59V.
Min safe supply voltage = 9.03V to 9.39V.

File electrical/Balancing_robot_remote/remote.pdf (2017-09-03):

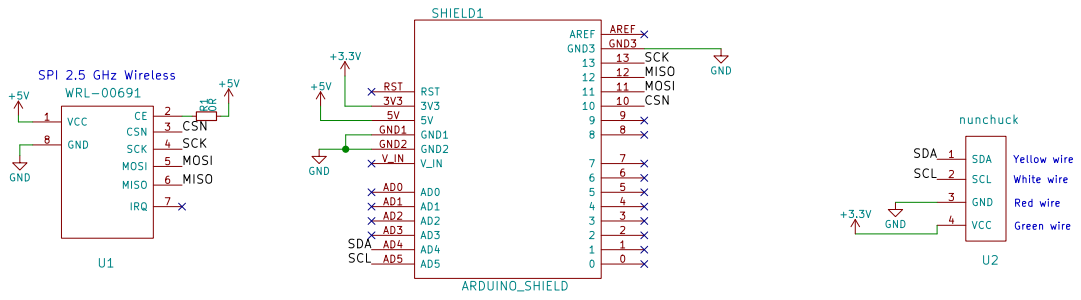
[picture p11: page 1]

Yellow wire White wire Red wire Green wire

Id: 1/1 Title: File: remote.sch Sheet: /

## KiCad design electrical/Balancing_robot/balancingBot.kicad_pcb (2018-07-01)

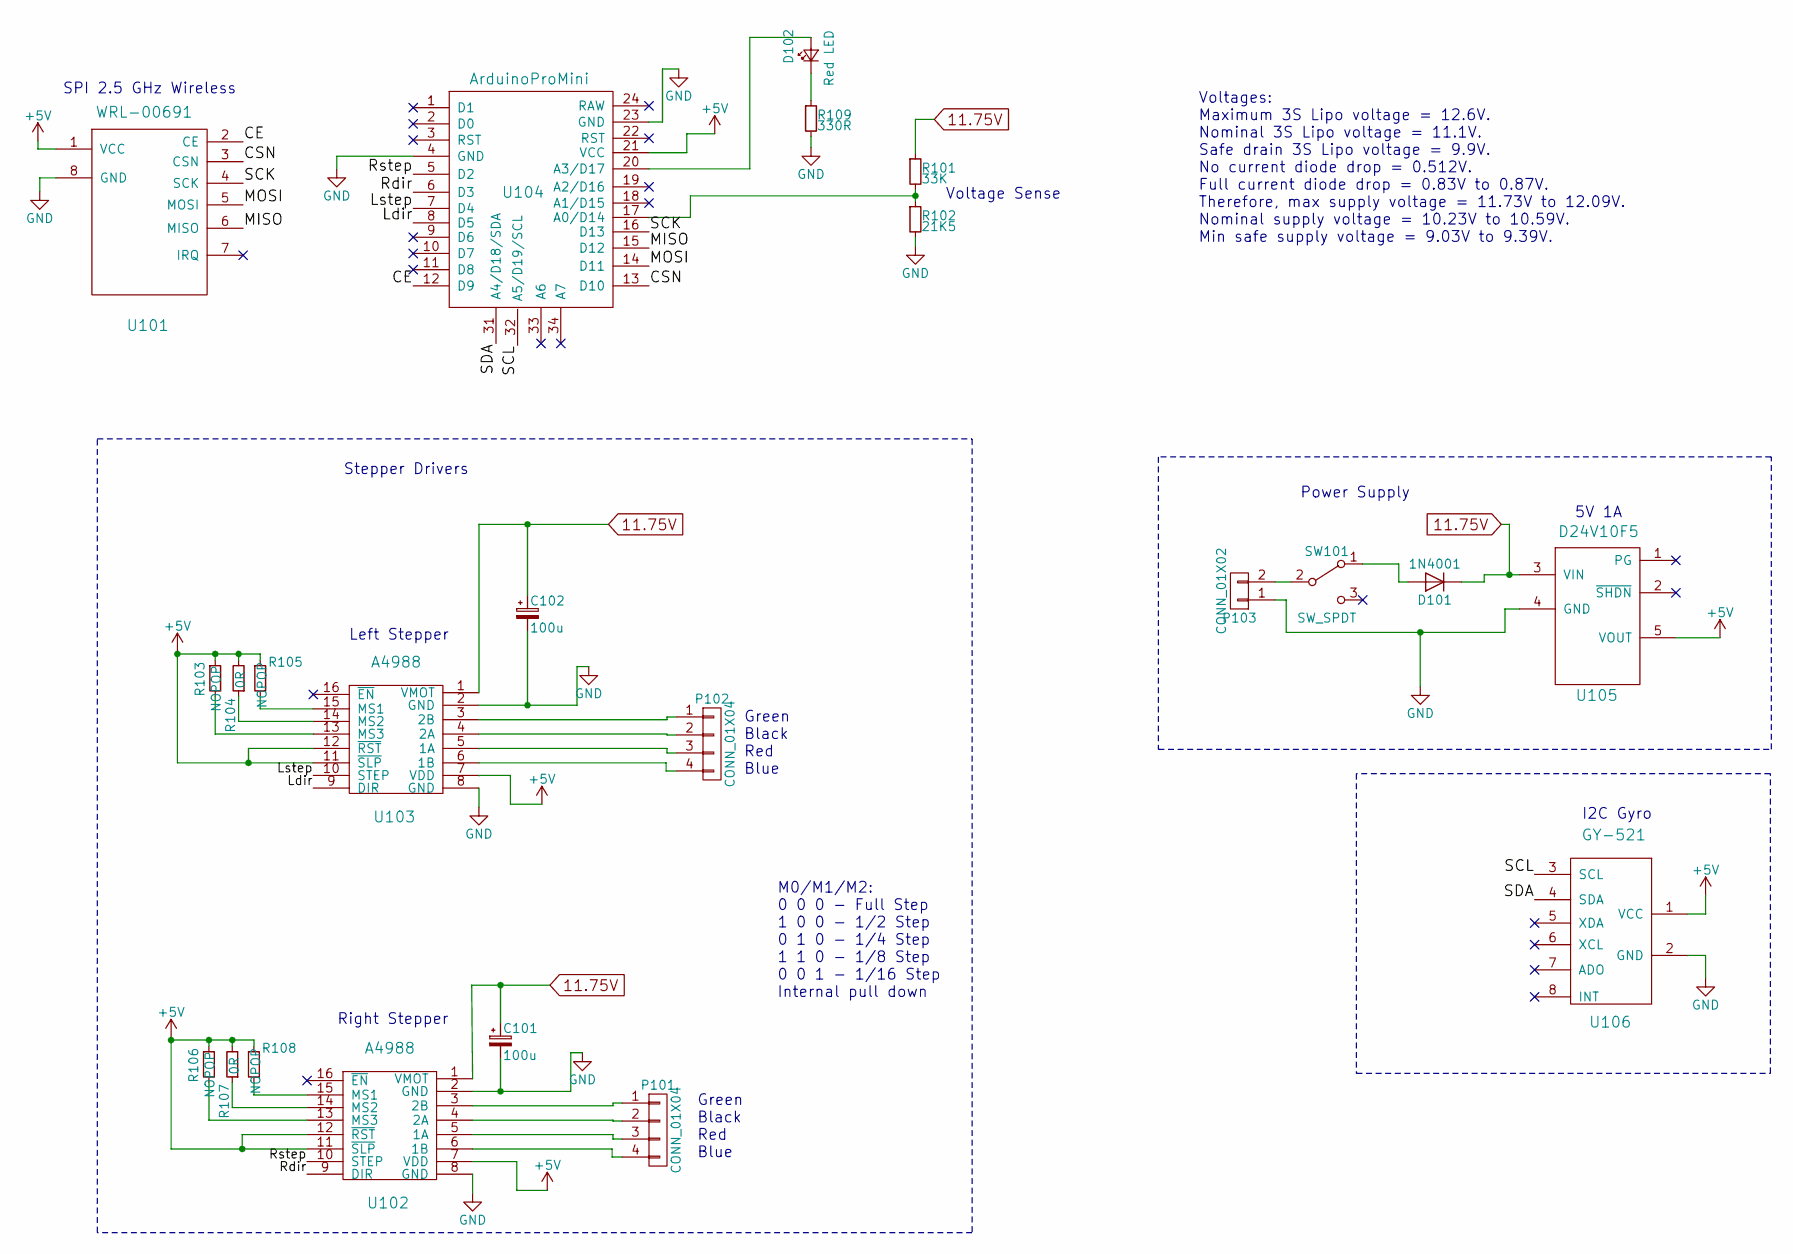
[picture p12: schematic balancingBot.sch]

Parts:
C101, C102: 100u; C_Radial_D7.5_L11.2_P2.5
D101: 1N4001; Diode_DO-41_SOD81_Horizontal_RM10
D102: Red LED; LED_0805_HandSoldering
P101, P102: CONN_01X04; Pin_Header_Straight_1x04
P103: CONN_01X02; Terminal_Block_200_mil
R101: 33K; R_0805_HandSoldering
R102: 21K5; R_0805_HandSoldering
R103, R105, R106, R108: NOPOP; R_0805_HandSoldering
R104, R107: 0R; R_0805_HandSoldering
R109: 330R; R_0805_HandSoldering
SW101: SW_SPDT; SWITCH-200MSP1T1B1M2QEH
U101: WRL-00691
U102, U103: A4988
U104: ArduinoProMini; Arduino_Pro_Mini
U105: D24V10F5
U106: GY-521

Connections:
11.75V: C101.1, C102.1, D101.1 (K), R101.1, U102.1 (VMOT), U103.1 (VMOT), U105.3 (VIN)
+5V: R103.1, R104.2, R105.1, R106.1, R107.2, R108.1, U101.1 (VCC), U102.7 (VDD), U102.11 (~SLP), U102.12 (~RST), U103.7 (VDD), U103.11 (~SLP), U103.12 (~RST), U104.21 (VCC), U105.5 (VOUT), U106.1 (VCC)
/CE: U101.2 (CE), U104.12 (D9)
/CSN: U101.3 (CSN), U104.13 (D10)
/Ldir: U103.9 (DIR), U104.8 (D5)
/Lstep: U103.10 (STEP), U104.7 (D4)
/MISO: U101.6 (MISO), U104.15 (D12)
/MOSI: U101.5 (MOSI), U104.14 (D11)
/Rdir: U102.9 (DIR), U104.6 (D3)
/Rstep: U102.10 (STEP), U104.5 (D2)
/SCK: U101.4 (SCK), U104.16 (D13)
/SCL: U104.32 (A5/D19/SCL), U106.3 (SCL)
/SDA: U104.31 (A4/D18/SDA), U106.4 (SDA)
GND: C101.2, C102.2, P103.1, R102.2, R109.2, U101.8 (GND), U102.2 (GND), U102.8 (GND), U103.2 (GND), U103.8 (GND), U104.4 (GND), U104.23 (GND), U105.4 (GND), U106.2 (GND)
unnamed: D101.2 (A), SW101.1 (A)
unnamed: D102.1 (K), R109.1
unnamed: D102.2 (A), U104.20 (A3/D17)
unnamed: P101.1, U102.3 (2B)
unnamed: P101.2, U102.4 (2A)
unnamed: P101.3, U102.5 (1A)
unnamed: P101.4, U102.6 (1B)
unnamed: P102.1, U103.3 (2B)
unnamed: P102.2, U103.4 (2A)
unnamed: P102.3, U103.5 (1A)
unnamed: P102.4, U103.6 (1B)
unnamed: P103.2, SW101.2 (B)
unnamed: R101.2, R102.1, U104.17 (A0/D14)
unnamed: R103.2, U103.13 (MS3)
unnamed: R104.1, U103.14 (MS2)
unnamed: R105.2, U103.15 (MS1)
unnamed: R106.2, U102.13 (MS3)
unnamed: R107.1, U102.14 (MS2)
unnamed: R108.2, U102.15 (MS1)

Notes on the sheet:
Right Stepper
Left Stepper
I2C Gyro
SPI 2.5 GHz Wireless
5V 1A
M0/M1/M2: 0 0 0 - Full Step 1 0 0 - 1/2 Step 0 1 0 - 1/4 Step 1 1 0 - 1/8 Step 0 0 1 - 1/16 Step Internal pull down
Voltage Sense
Power Supply
Stepper Drivers
Voltages: Maximum 3S Lipo voltage = 12.6V. Nominal 3S Lipo voltage = 11.1V. Safe drain 3S Lipo voltage = 9.9V. No current diode drop = 0.512V. Full current diode drop = 0.83V to 0.87V. Therefore, max supply voltage = 11.73V to 12.09V. Nominal supply voltage = 10.23V to 10.59V. Min safe supply volta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
Green Black Red Blue

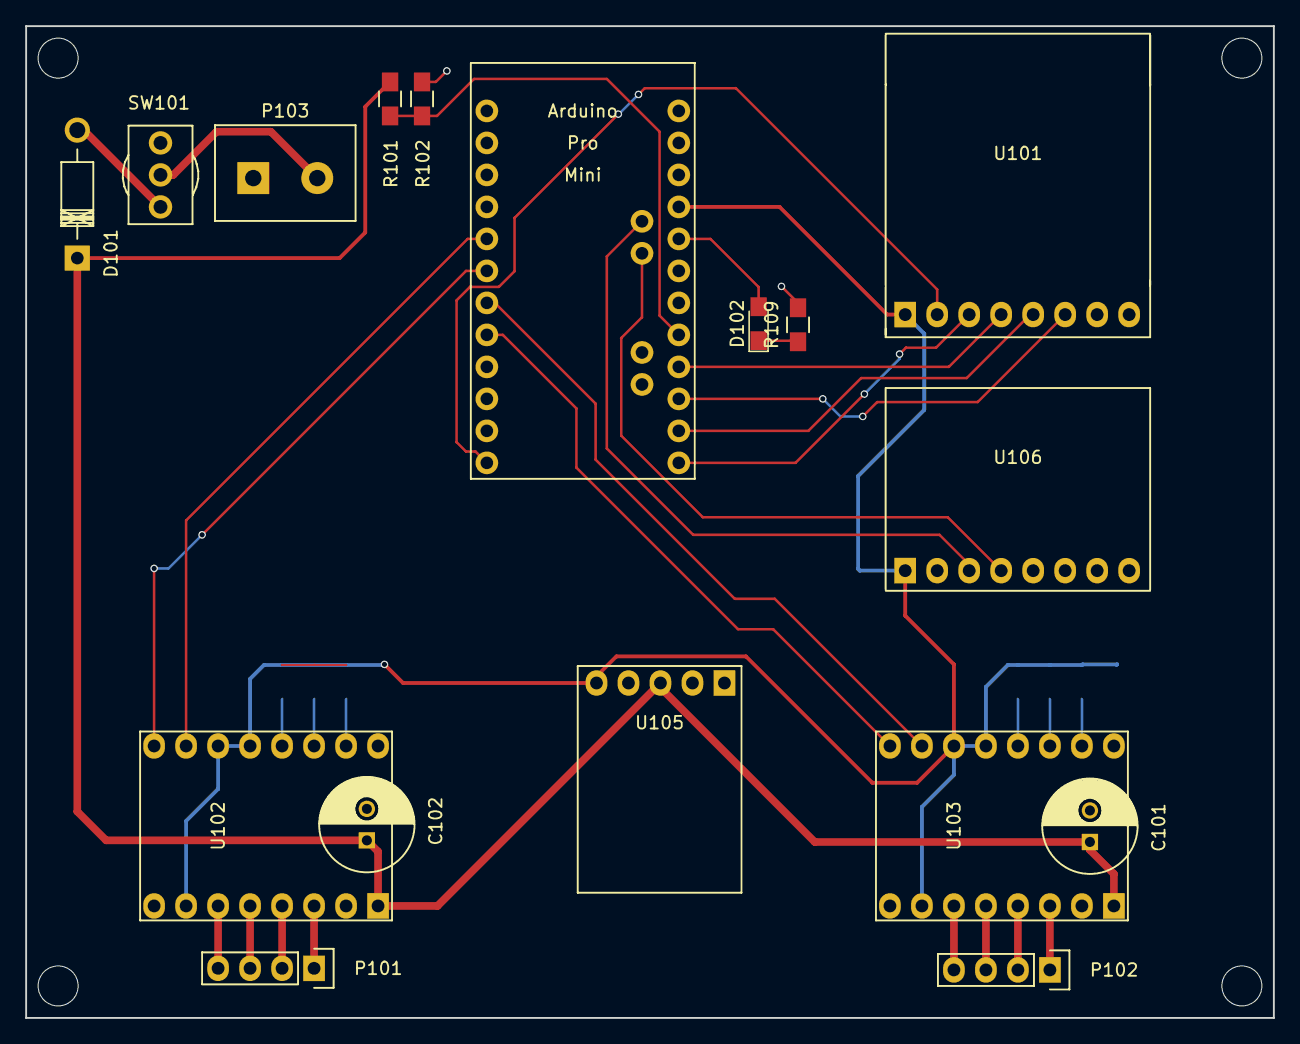
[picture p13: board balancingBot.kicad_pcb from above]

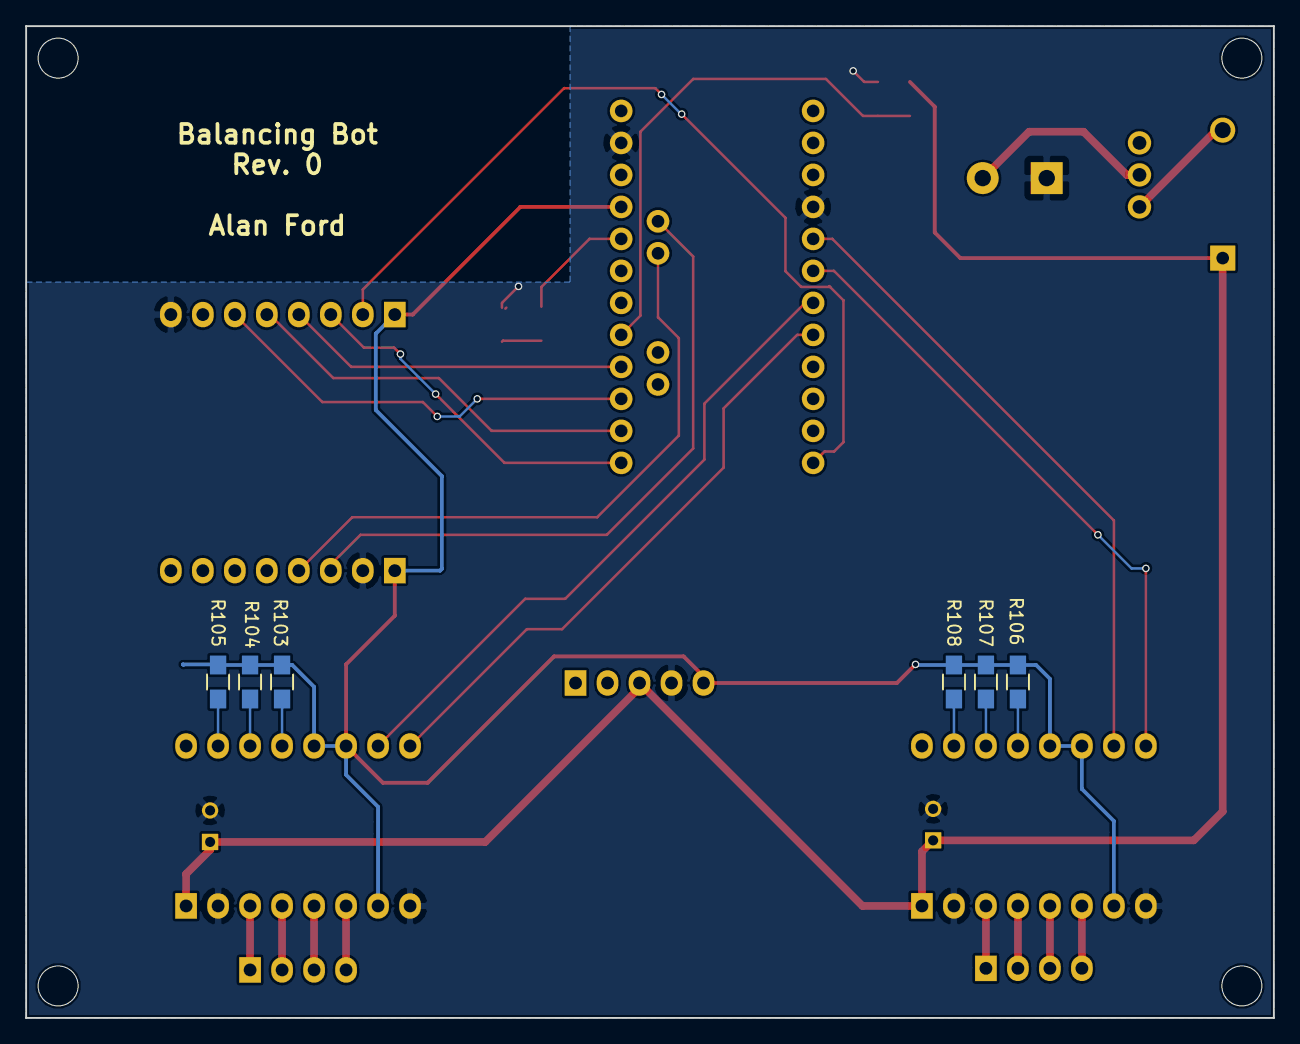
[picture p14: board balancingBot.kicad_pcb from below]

Board: 2 copper layers, 99.1 x 78.7 mm, 23 parts (6 on the bottom side), 33 nets.

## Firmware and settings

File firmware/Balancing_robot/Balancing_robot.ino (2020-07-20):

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
// #define BR_DEBUG

#include <Wire.h>   //Include the Wire.h library so we can communicate with the gyro over I2C

#include "RF24.h"   //from the RF24 Arduino library

#include "limits.h"

///////////////////////////////////////////////////////////////////////////////////////
// Define a data structure used to pass data to the  direction_control() function
///////////////////////////////////////////////////////////////////////////////////////
struct control_params {
  float pid_output_left;
  float pid_output_right;
  float pid_setpoint;
};


///////////////////////////////////////////////////////////////////////////////////////
// User Config for the GPIO Pins
// Other pins (such as I2C, UART, and SPI pins) may be used internally by various libraries
///////////////////////////////////////////////////////////////////////////////////////
const int RIGHTMOTORSTEP_PIN   =  2;
const int RIGHTMOTORDIR_PIN    =  3;
const int LEFTMOTORSTEP_PIN    =  4;
const int LEFTMOTORDIR_PIN     =  5;
const int RADIO_CHIP_ENABLE_PIN = 9;
const int RADIO_CHIP_SELECT_PIN = 10;
const int LED_PIN = 17;

///////////////////////////////////////////////////////////////////////////////////////
// Radio signal data for bot control
// These are the data values that can be received from the remote control
///////////////////////////////////////////////////////////////////////////////////////
const byte TURN_LEFT = B00000001;
const byte TURN_RIGHT = B00000010;
const byte MOVE_FORWARD = B00000100;
const byte MOVE_REVERSE = B00001000;
const byte STABILIZE = B00001100;


///////////////////////////////////////////////////////////////////////////////////////
// pin definitions for stepper motor controls
// These are used as masks to set bits in output registers
///////////////////////////////////////////////////////////////////////////////////////
const uint8_t LEFTMOTORDIR     = (0b00000001 << LEFTMOTORDIR_PIN);
const uint8_t LEFTMOTORSTEP    = (0b00000001 << LEFTMOTORSTEP_PIN);
const uint8_t RIGHTMOTORDIR    = (0b00000001 << RIGHTMOTORDIR_PIN);
const uint8_t RIGHTMOTORSTEP   = (0b00000001 << RIGHTMOTORSTEP_PIN);

///////////////////////////////////////////////////////////////////////////////////////
// a string used to communicate with the intended remote control receiver
///////////////////////////////////////////////////////////////////////////////////////
const byte radio_address[] = "1robt";

////////////////////////////////////////////////////////
///  \brief MPU-6050 I2C address (0x68 or 0x69).
////////////////////////////////////////////////////////
const int gyro_address = 0x68;

////////////////////////////////////////////////////////
///  \brief accelerometer calibration bias value that is
///  dependent on the physical mounting of the gyro.
///  This should be updated for each physical robot
////////////////////////////////////////////////////////
const int acc_calibration_value = -503;

////////////////////////////////////////////////////////
///  \brief Gain setting for the P-controller (15).
////////////////////////////////////////////////////////
const float pid_p_gain = 15;
////////////////////////////////////////////////////////
///  \brief Gain setting for the I-controller (1.5).
////////////////////////////////////////////////////////
const float pid_i_gain = 1.5;
////////////////////////////////////////////////////////
///  \brief Gain setting for the D-controller (30).
////////////////////////////////////////////////////////
const float pid_d_gain = 30;



////////////////////////////////////////////////////////
///  \brief Turning velocity in units of  (30).
////////////////////////////////////////////////////////
const float turning_speed = 30;

////////////////////////////////////////////////////////
///  \brief Target maximum velocity in units of  (150).
////////////////////////////////////////////////////////
const float max_target_speed = 150;

////////////////////////////////////////////////////////
///  Global Variables
////////////////////////////////////////////////////////

////////////////////////////////////////////////////////
//  used by the primary timing routine
//  Initialized in setup()
//  Used in loop()
////////////////////////////////////////////////////////
unsigned long start_time;
////////////////////////////////////////////////////////
///  \brief The time required for each program loop in microsec.
////////////////////////////////////////////////////////
const int loop_time_us = 4000;


/////////////////////////////////////////////////////////
// Calibration parameters set in setup() and used in loop()
////////////////////////////////////////////////////////
long gyro_yaw_calibration_value;
long gyro_pitch_calibration_value;

///////////////////////////////////////////////////////////////////////////////////////
// Variables for motor pulse calculations
// Values are determined in calculate_motor_pulse_interval()
// and used in the ISR() interrupt service routine
// These are marked volatile because their
// values can be changed by something beyond the control of the code section in which they appear
///////////////////////////////////////////////////////////////////////////////////////
volatile int throttle_left_motor;
volatile int throttle_right_motor;

///////////////////////////////////////////////////////////////////////////////////////
// User Config For the Radio
// Hardware configuration: Set up nRF24L01 radio on SPI bus plus two additional pins
///////////////////////////////////////////////////////////////////////////////////////
RF24 radio(RADIO_CHIP_ENABLE_PIN, RADIO_CHIP_SELECT_PIN);




///////////////////////////////////////////////////////////////////////////////////////////////////////////////////////////////////////
//Setup basic functions
///////////////////////////////////////////////////////////////////////////////////////////////////////////////////////////////////////
void setup() {
#ifdef BR_DEBUG
  Serial.begin(9600);
#endif

  // set input/output modes for gpio pins
  pinMode(RIGHTMOTORSTEP_PIN, OUTPUT);
  pinMode(RIGHTMOTORDIR_PIN, OUTPUT);
  pinMode(LEFTMOTORSTEP_PIN, OUTPUT);
  pinMode(LEFTMOTORDIR_PIN, OUTPUT);
  pinMode(LED_PIN, OUTPUT);

  // I2C will be used to communicate with the gyro
  initialize_i2c();
  initialize_gyro();

  // setting LED_PIN to OUTPUT >>MUST<<
  // be completed before calling calibrate_gyro()
  // because gyro() will use it!
  calibrate_gyro();

  // Note: the radio uses the SPI bus
  initialize_radio();

  // Timer is used to by interrupt service to control the motors
  initialize_timer();
  start_time = micros();

}

///////////////////////////////////////////////////////////////////////////////////////////////////////////////////////////////////////
//Main program loop
///////////////////////////////////////////////////////////////////////////////////////////////////////////////////////////////////////
void loop() {
  bool reset_pid;
  float angle_acc;
  byte received_byte = 0;
  static byte low_bat_flag = 0;
  static byte start_flag = 0;
  static float pid_output;
  static control_params control_parameters;
  static float angle_gyro;
  static float self_balance_pid_setpoint;
  unsigned long current_time;
  if ( battery_voltage_is_low() ) {
    digitalWrite(LED_PIN, HIGH);       //Turn on the led if battery voltage is to low
    low_bat_flag = 1;                  //Set the low_bat_flag variable to 1
  }

  angle_acc = get_accelerometer_angle();

  if (start_flag == 0 && angle_acc > -0.5 && angle_acc < 0.5) { //If the accelerometer angle is almost 0
    angle_gyro = angle_acc;                                    //Load the accelerometer angle in the angle_gyro variable
    start_flag = 1;                                            //Set the start variable to start the PID controller
  }

  get_gyro_angle(angle_acc, angle_gyro);

  if (angle_gyro > 30 || angle_gyro < -30 || start_flag == 0 || low_bat_flag == 1) {  //If the robot tips over or the start variable is zero or the battery is empty
    reset_pid = true;
    start_flag = 0;                                                              //Set the start variable to 0
    self_balance_pid_setpoint = 0;                                          //Reset the self_balance_pid_setpoint variable
  }
  else {
    reset_pid = false;
  }
  pid_output = pid_calculator(reset_pid, pid_output, control_parameters.pid_setpoint, angle_gyro, self_balance_pid_setpoint);

  received_byte = get_radio_data();
  direction_control(pid_output, received_byte, control_parameters);

  //The self balancing point is adjusted when there is not forward or backwards movement from the transmitter. This way the robot will always find it's balancing point
  if (control_parameters.pid_setpoint == 0) {                                                  //If the setpoint is zero degrees
    if (pid_output < 0)self_balance_pid_setpoint += 0.0015;                 //Increase the self_balance_pid_setpoint if the robot is still moving forewards
    if (pid_output > 0)self_balance_pid_setpoint -= 0.0015;                 //Decrease the self_balance_pid_setpoint if the robot is still moving backwards
  }

  calculate_motor_pulse_interval(control_parameters.pid_output_left, control_parameters.pid_output_right);


  ///////////////////////////////////////////////////////////////////////////////////////////////////////////////////////////////////////
  //Loop time timer
  // wait in a loop until "loop_time_us" microseconds has elapsed
  ///////////////////////////////////////////////////////////////////////////////////////////////////////////////////////////////////////
  do {
    current_time = micros();
  } while (current_time - start_time < loop_time_us);
  start_time = current_time;
}

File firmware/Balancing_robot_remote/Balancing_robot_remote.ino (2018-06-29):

// TODO:  why read 6 bytes from the nunchuck when 4 will do?
// TODO:  do we really need to set TWBR when initallizing I2C?  The library seems to do it already.
// TODO:  implement BOT_STABLE
///////////////////////////////////////////////////////////////////////////////////////
// Wiring Configuration for the Build,RVA Version
// Arduinio UNO
//
// Arduino                      Nunchuck (Your wire colors may be different)
// A4                           SDA (yellow)
// A5                           SCL (white)
// GND                          GND (red)
// +3.3V                        VCC (green)
//
// Arduino                      Radio
// D9                           CE
// D10                          CSN
// D11                          MOSI
// D12                          MISO
// D13                          SCK
// +5V                          VCC
// GND                          GND
//
///////////////////////////////////////////////////////////////////////////////////////
//   Nunchuck Wiring
//   Note that the wiring colors may vary from what is documented here,
//   depending on the hardware vendor.
//
//   Nunchuck Wiring (looking into the nunchuck connector):
//
//   white(scl)                   red(gnd)
//   -----------                 -------------
//   |         |                 |           |
//   |         | ----------------|           |
//   |                                       |
//   |---------------------------------------|
//   green(vcc)   black(detect)   yellow(sda)
//
//   I2C data: see http://dangerousprototypes.com/blog/2009/08/19/bus-pirate-wii-nunchuck-quick-guide/
//   http://robotshop.com/letsmakerobots/wii-nunchuckarduino-tutorial
//   https://create.arduino.cc/projecthub/infusion/using-a-wii-nunchuk-with-arduino-597254
//
///////////////////////////////////////////////////////////////////////////////////////

#include <Wire.h>   //Include the Wire.h library so we can communicate with the Nunchuck
#include <SPI.h>    //Include the SPI.h library for the radio
#include "RF24.h"   //Don't know where this is coming from, but it's for the radio
#include <printf.h>

///////////////////////////////////////////////////////////////////////////////////////
// User Config For the Radio
// Hardware configuration: Set up nRF24L01 radio on SPI bus plus pins 9 & 10
RF24 radio(9,10);
byte radio_address[] = "1robt";         // this is the "pipe" we will be using
///////////////////////////////////////////////////////////////////////////////////////

///////////////////////////////////////////////////////////////////////////////////////
// User Config for the Nunchuck
#define NUNCHUCK_ADDR 0x52                            //Nunchuk I2C address (0x52)
#define LOW_DEADZONE 80
#define HIGH_DEADZONE 170
byte received_data[6], send_byte;                                   //Declare some global byte variables
///////////////////////////////////////////////////////////////////////////////////////

///////////////////////////////////////////////////////////////////////////////////////
// Radio signal data for bot control
#define RADIO_NULL  B00000000
#define BOT_LEFT    B00000001
#define BOT_RIGHT   B00000010
#define BOT_FORWARD B00000100
#define BOT_REVERSE B00001000
#define BOT_STABLE  B00001100
///////////////////////////////////////////////////////////////////////////////////////


void setup(){
  initialize_serial();
  initialize_radio();
  initialize_I2C();
  wake_nunchuck();
}

void loop(){
  bool status;
  Wire.beginTransmission(NUNCHUCK_ADDR  );                          //Start communication with the Nunchuck.
  Wire.write(0x00);                                                 //We want to start reading at register (00 hex)
  Wire.endTransmission();                                           //End the transmission
  Wire.requestFrom(NUNCHUCK_ADDR,6);                                //Request 6 bytes from the Nunchuck
  for(byte i = 0; i < 6; i++) received_data[i] = Wire.read();       //Copy the bytes to the received_data array
  send_byte = RADIO_NULL;                                           //Set the send_byte variable to 0
  if(received_data[0] < LOW_DEADZONE)                               //Turn left
    send_byte |= BOT_LEFT;                                          //If the variable received_data[0] is smaller then 80 set bit 0 of the send byte variable
  if(received_data[0] > HIGH_DEADZONE)                              //Turn right
    send_byte |= BOT_RIGHT;                                         //If the variable received_data[0] is larger then 170 set bit 1 of the send byte variable
  if(received_data[1] < LOW_DEADZONE)                               //Roll backwards
    send_byte |= BOT_REVERSE;                                       //If the variable received_data[1] is smaller then 80 set bit 3 of the send byte variable
  if(received_data[1] > HIGH_DEADZONE)                              //Roll forward
    send_byte |= BOT_FORWARD;                                       //If the variable received_data[1] is larger then 170 set bit 2 of the send byte variable
  if (send_byte)
  {
    radio.write(&send_byte,sizeof(send_byte));                       //Send the send_byte variable if it's value is larger then 0
  }
  delay(40);                                                        //Create a 40 millisecond loop delay
}

void initialize_radio() {
  if (!radio.begin())                                               //Start the SPI nRF24L01 radio
  {
    Serial.println("Error: Radio failed to initialize");                                                    
  }
  radio.stopListening();                                            // prepare to open a pipe for writing
  radio.openWritingPipe(radio_address);                             // Open a writing pipe on the radio
}

void initialize_serial(){
  Serial.begin(9600);                                               //Start the serial port at 9600 kbps
  printf_begin();
}

void initialize_I2C() {
  Wire.begin();                                                             //Start the I2C bus as master
  //  disable the on-chip pull-ups and rely on the nunchuk pull-ups
  digitalWrite(SCL, LOW);
  digitalWrite(SDA, LOW);
  //TWBR = 12;                                                                //Set the I2C clock speed to 400kHz
  delay(20);                                                                //Short delay
}
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

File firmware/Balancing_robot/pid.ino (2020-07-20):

float pid_calculator(bool reset, float pid_output, float pid_setpoint, float angle_gyro, float self_balance_pid_setpoint) {
  float pid_error_temp;
  static float pid_i_mem = 0;
  static float pid_last_d_error = 0;
  if (reset ) {
    pid_output = 0;                                                         //Set the PID controller output to 0 so the motors stop moving
    pid_i_mem = 0;
    pid_last_d_error = 0;                                                         //Reset the I-controller memory
  }
  else {
    ///////////////////////////////////////////////////////////////////////////////////////////////////////////////////////////////////////
    //PID controller calculations
    ///////////////////////////////////////////////////////////////////////////////////////////////////////////////////////////////////////
    //The balancing robot is angle driven. First the difference between the desired angle (setpoint) and actual angle (process value)
    //is calculated. The self_balance_pid_setpoint variable is automatically changed to make sure that the robot stays balanced all the time.
    //The (pid_setpoint - pid_output * 0.015) part functions as a brake function.
    pid_error_temp = angle_gyro - self_balance_pid_setpoint - pid_setpoint;
    if (pid_output > 10 || pid_output < -10)pid_error_temp += pid_output * 0.015 ;

    pid_i_mem += pid_i_gain * pid_error_temp;                                 //Calculate the I-controller value and add it to the pid_i_mem variable
    //if (pid_i_mem > 400)pid_i_mem = 400;                                      //Limit the I-controller to the maximum controller output
    //else if (pid_i_mem < -400)pid_i_mem = -400;
    //Calculate the PID output value
    pid_output = pid_p_gain * pid_error_temp + pid_i_mem + pid_d_gain * (pid_error_temp - pid_last_d_error);
    //if (pid_output > 400)pid_output = 400;                                    //Limit the PI-controller to the maximum controller output
    //else if (pid_output < -400)pid_output = -400;

    pid_last_d_error = pid_error_temp;                                        //Store the error for the next loop

    if (pid_output < 5 && pid_output > -5)pid_output = 0;                     //Create a dead-band to stop the motors when the robot is balanced

  }
  return pid_output;
}

void direction_control(float pid_output, byte received_byte, control_params &control_parameters) {
  ///////////////////////////////////////////////////////////////////////////////////////////////////////////////////////////////////////
  //Direction Control calculations
  ///////////////////////////////////////////////////////////////////////////////////////////////////////////////////////////////////////
  control_parameters.pid_output_left = pid_output;                                             //Copy the controller output to the pid_output_left variable for the left motor
  control_parameters.pid_output_right = pid_output;                                            //Copy the controller output to the pid_output_right variable for the right motor

  if (received_byte & TURN_LEFT) {                                          //If the first bit of the receive byte is set change the left and right variable to turn the robot to the left
    control_parameters.pid_output_left += turning_speed;                                       //Increase the left motor speed
    control_parameters.pid_output_right -= turning_speed;                                      //Decrease the right motor speed
  }
  if (received_byte & TURN_RIGHT) {                                          //If the second bit of the receive byte is set change the left and right variable to turn the robot to the right
    control_parameters.pid_output_left -= turning_speed;                                       //Decrease the left motor speed
    control_parameters.pid_output_right += turning_speed;                                      //Increase the right motor speed
  }

  if (received_byte & MOVE_FORWARD) {                                          //If the third bit of the receive byte is set change the left and right variable to move the robot forward
    if (control_parameters.pid_setpoint > -2.5)control_parameters.pid_setpoint -= 0.05;                           //Slowly change the setpoint angle so the robot starts leaning forewards
    if (pid_output > max_target_speed * -1)control_parameters.pid_setpoint -= 0.005;           //Slowly change the setpoint angle so the robot starts leaning forewards
  }
  if (received_byte & MOVE_REVERSE) {                                          //If the forth bit of the receive byte is set change the left and right variable to move the robot backward
    if (control_parameters.pid_setpoint < 2.5)control_parameters.pid_setpoint += 0.05;                            //Slowly change the setpoint angle so the robot starts leaning backwards
    if (pid_output < max_target_speed)control_parameters.pid_setpoint += 0.005;                //Slowly change the setpoint angle so the robot starts leaning backwards
  }

  if (!(received_byte & STABILIZE)) {                                       //Slowly reduce the setpoint to zero if no foreward or backward command is given
    if (control_parameters.pid_setpoint > 0.5)control_parameters.pid_setpoint -= 0.05;                            //If the PID setpoint is larger then 0.5 reduce the setpoint with 0.05 every loop
    else if (control_parameters.pid_setpoint < -0.5)control_parameters.pid_setpoint += 0.05;                      //If the PID setpoint is smaller then -0.5 increase the setpoint with 0.05 every loop
    else control_parameters.pid_setpoint = 0;                                                  //If the PID setpoint is smaller then 0.5 or larger then -0.5 set the setpoint to 0
  }
}

/////////////////////////////////////////////////////////////////////////////////////////////
// convert the pid speed value to a pulse interval
// if pid speed value is 0, set the pulse interval to 0 (special value for ISR)
// if |pulse interval| > MAX_PULSE_INTERVAL, limit pulse interval to +/- MAX_PULSE_INTERVAL
// if |pulse interval| < MIN_PULSE_INTERVAL, limit pulse interval to +/- MIN_PULSE_INTERVAL
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

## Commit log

2017-07-31 modifying the firmware to usie SPI instead of serial for the radio
2017-07-31 added caps to motor driver and changed diode to 1N4001
    [balancingBot.sch]
2017-07-31 organized schematic
    [balancingBot.sch]
2017-07-31 corrected SPI connections
    [balancingBot.sch]
2017-07-31 reorganized directory structure
    [balancingBot.kicad_pcb, balancingBot.sch]
2017-07-31 added schematic for remote
    [remote.sch]
2017-07-31 added nunchuck wire colors
    [remote.sch]
2017-09-03 tweeked the schematic
    [balancingBot.sch, remote.sch]
2017-09-04 converted to pcb and initial pcb layout
    [balancingBot.kicad_pcb, balancingBot.sch]
2017-09-09 created gerbers
    [balancingBot-B.Cu.gbl, balancingBot-B.Mask.gbs, balancingBot-B.SilkS.gbo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]
2017-10-16 working on the firmware tests
    [balancingBot.sch, battery monitor.xlsx, motor control.xlsx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]
2017-10-29 added docs and spreadsheet for motor feedback analysis
    [motor control.xlsx]
2018-05-31 finally,delayed update with a working bot
    [balancingBot.sch]
2018-06-13 refreshing after being a slacker
    [BOM.xlsx, Balancing_Robot.xlsx]
2018-06-16 modified schematics to connect radio CE pin to pin D9 on the arduinos
    [balancingBot.sch, remote.sch]
2018-06-16 updated battery voltage calculation to reflect millivolts
2018-06-18 first failed attempt at right/left fix
    [Balancing_robot.ino]
2018-06-19 updated pcb to include status LED, associated resistor, and radio enable line
    [balancingBot.kicad_pcb, balancingBot.sch]
2018-06-20 straightened out the left-right confusion and which motor used which pins
2018-06-22 removed serial comm option for the radio and made the SPI option the default
2018-06-27 added debug print for battery voltage
2018-06-27 rerouted power and moved traces hidden by daughter boards
    [balancingBot.kicad_pcb]
2018-06-27 updated documentation to describe the motor current limits needed for this design
2018-06-29 disabled arduino internal pull-up resistors on I2C lines
2018-06-29 clean up docs and started a spreadsheet to model the PID controller
    [newMath.xlsx]
2018-07-01 changed stepper drivers to A4988 on pcb and schematic
    [balancingBot.kicad_pcb, balancingBot.sch]
2018-07-01 updated the documentation to describe the A4988 motor drivers
2018-07-02 updated docs with a discussion of battery voltage and fixed a battery voltage typo in the bot firmware
    [Balancing_robot.ino]
2020-05-26 cleaned up file structure
    [Balancing_Robot.xlsx, battery monitor.xlsx, motor control.xlsx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]
2020-06-07 added volatile to variables used by the interrupt routine and paused interrupts when accessing them outside of the interrupt service routine.
2020-07-05 corrected the battery voltage calculation
    [misc.ino]
2020-07-05 adjusted accelerometer angle conversion
2020-07-20 simplified the motor pulse interval calculations
    [newMath.xlsx]
